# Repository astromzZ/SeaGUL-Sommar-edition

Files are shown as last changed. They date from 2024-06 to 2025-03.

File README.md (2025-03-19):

# Seagul - Chalmers undervattensglidare
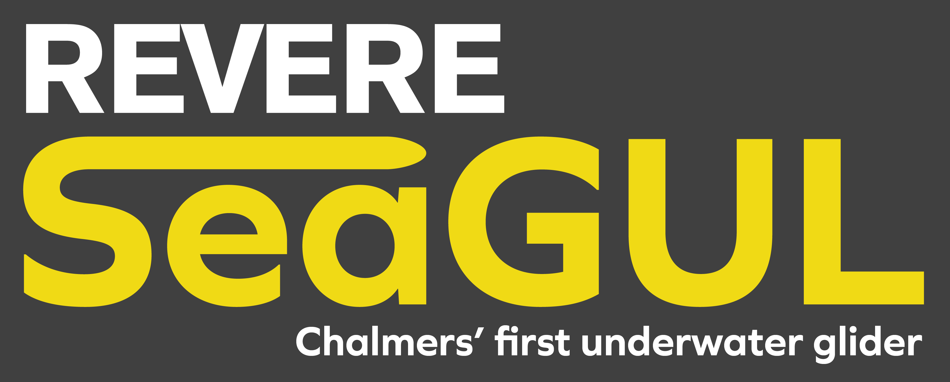
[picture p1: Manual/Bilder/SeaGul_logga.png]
Logga


This repository is for Chalmers underwater glider SEAgul. Here you will find code, instructions and construction files for the glider.

Before handling the glider, make sure to read thorugh the manual. 

The most recent CAD files can be found [here](https://drive.google.com/drive/folders/1H2lXxEGizccBVgk5y8HHm3Ga0hIDHSA2?usp=drive_link).

Contact information:

Oskar Andersson - Oskar.simon.andersson@gmail.com (Programming, CAD)

Peo Gradin - peo.gradin@live.se (Electronics, Programming)

Joel Janson - joeljanson19@gmail.com (Hardware)

Cevin Åström - cevinastrom87@gmail.com (Programming)

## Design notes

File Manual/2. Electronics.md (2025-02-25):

# Electronics

## Overview

he electronic system is divided into three custom-designed circuit boards, as well as several sensors and devices connected to them. The circuit boards are categorized as the "Control PCB," "Power PCB," and "Dropweight PCB." The Control PCB houses the microcontroller, SD card writer, stepper motor drivers, Solid State Relays (SSR) for the pump module, and a series of connectors for connecting the various system components. The Power PCB contains the DC-DC converters and outputs 24V, 3.3V, and 12V voltages. It also includes a voltage divider for measuring battery voltage. The Dropweight PCB technically didn’t need to be a separate circuit board, but it was created to simplify the development of the circuit boards and expedite the completion of the other boards without a finalized dropweight circuit design. The Dropweight PCB controls the electro-permanent magnet through either a signal or a voltage drop in the 3.3V line. The different PCBs and their functionality will be described below. The electronics designs have all been developed using Autodesk Fusion, and the files can be found in the *Electronic files* folder, possibly containing minor changes from the versions that were ordered and implemented in the glider.

## Control PCB

In this section, the control PCB will be presented and explained, hopefully to necessary extent for future improvements and user purposes. Below is an image of the control PCB taken from Autodesk Fusion.

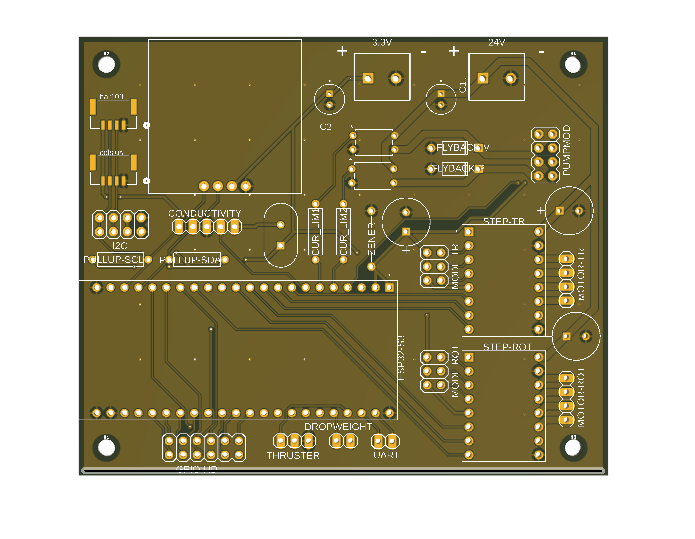
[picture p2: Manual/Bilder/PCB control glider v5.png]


And the schematic design, also from fusion, below.

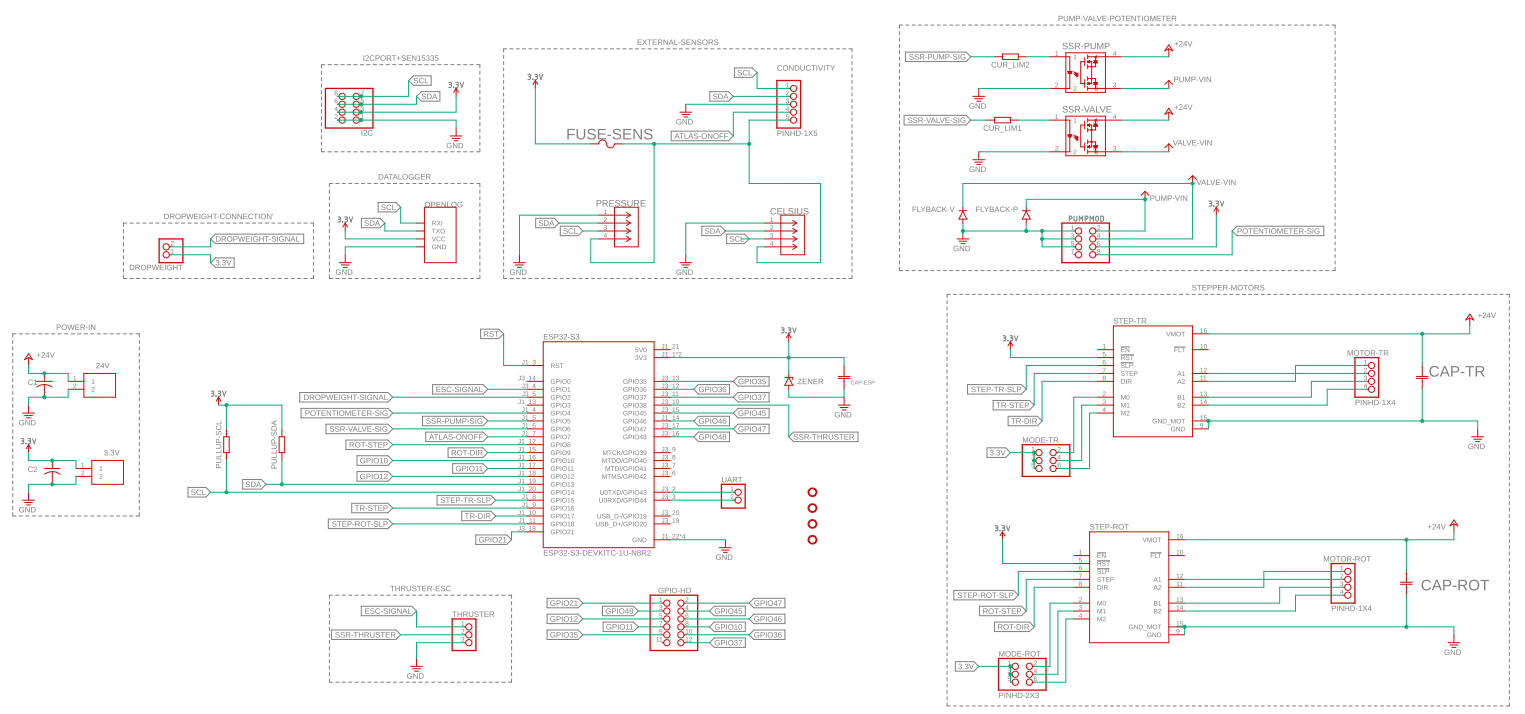
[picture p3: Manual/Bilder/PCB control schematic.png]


Finally we have an image of the control PCB mounted in the electronics bay with all the cable connections, taken shortly after the first water test at Voice of The Ocean (VOTO) with the new system. The USB cable is connected to the ESP32, but otherwise this setup is the same as when the glider is up and running.

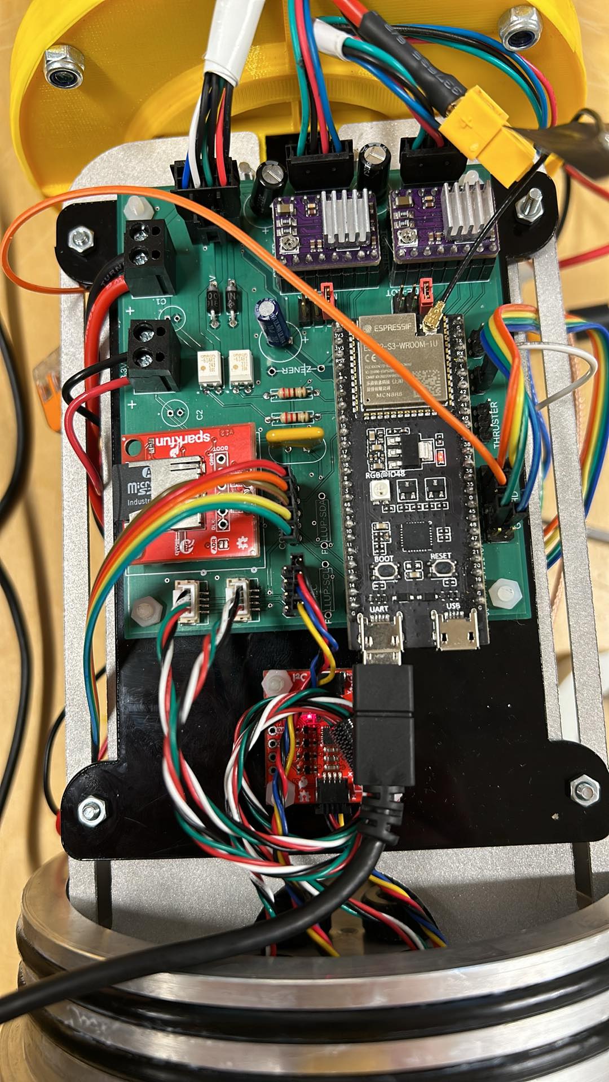
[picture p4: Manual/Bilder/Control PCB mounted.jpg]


### Microcontroller

The control PCB houses an ESP32-S3-DevkitC-N8R8, placed in pin header receptables for easy replacement, that functions as the brain of the system. In addition to communicating with all of the sensors and controlling motors, pump and so on, it also communicates with the Atlas Global Tracker (AGT) module. The AGT handles GPS and satellite communication for the glider, and communicates with the ESP via a Serial (UART) connection. The pinout on the ESP can be seen in the figure below.

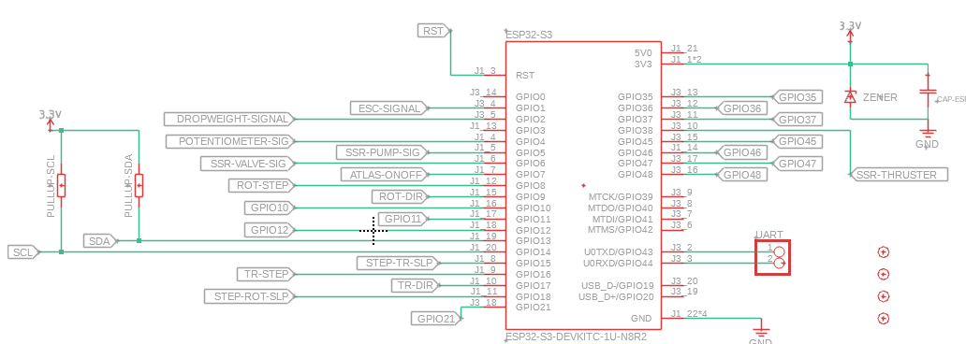
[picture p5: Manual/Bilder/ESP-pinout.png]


Some pins have specific names, and names for their headers, but many of them can be modified to be used for different functions. For example, the UART port can be configured and used as GPIO pins instead. Some other pins are directly traced to PCB mounted components, and not to pin headers, and thus their use can not be modified. An example of this would be the pins used for controlling the SSRs to the pump module. If any modification is to be done, it is advicable to follow the traces on the board in an EDA software, or in the images of this github manual, and make sure that it works as intended.

### GPIO header and other designated pin headers

There are som pins simply drawn out to pin headers on the circuit board, some which are designated for certain purposes and some unused. The GPIO header pinout can be seen in the image below

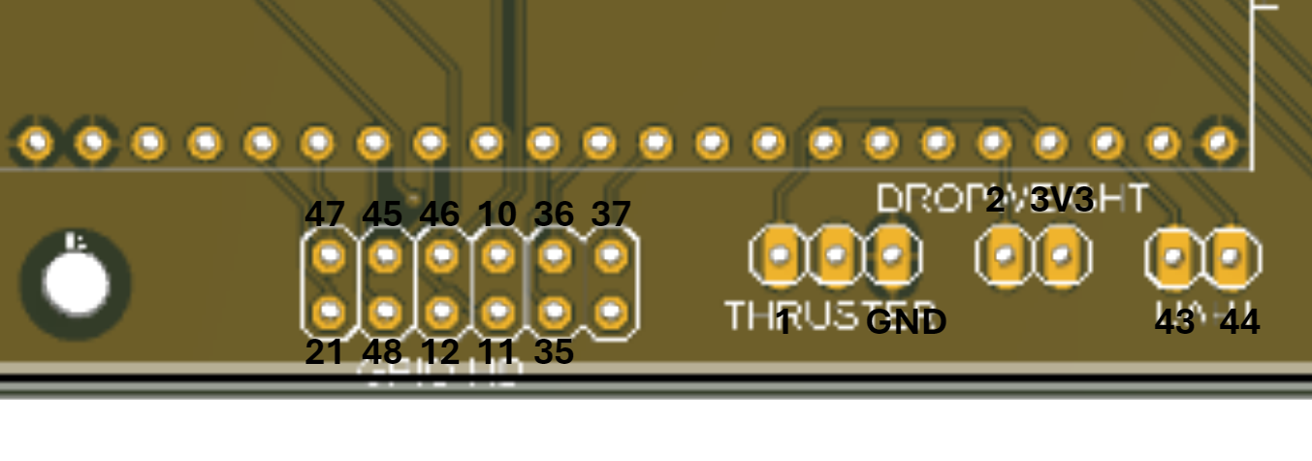
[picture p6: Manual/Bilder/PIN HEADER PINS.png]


where the connections for the thruster, dropweight and UART are also found. The numbers refer to the specific GPIO pin number from the ESP32. Unnamed pins in the image are simply not routed and can be ignored. The UART pins are unused as of now, but could connect to a UART device or be used as GPIO pins. The dropweight header has a signal pin, GPIO2, for the ESP32 to trigger the dropweight system, and also a 3V3 pin which can be used if the dropweight circuit is configured to be able to release the weight in the event of power failure. More on that in the description of the dropweight circuit.

Out of the general GPIO pin header, some are used for specific purposes listed below:

- **GPIO10** is used to read battery voltage, and this needs to be done from an ADC capable pin (preferrably ADC1 since ADC2 can be limited)

- **GPIO11** is sintended to be used to enable the voltage divider for reading VBAT, but is not implemented right now as one of the tranistors used in that circuitry did not work with 3.3V (Explained more in the *power PCB* section) and thus it is unused currently

- **GPIO12** is intended to be used for the SOS leak sensor, but not currently tested and implemented.

- **GPIO35 & 36** are used as Serial (UART) pins in communication between the ESP32 and the Atlas Global Tracker. 35 (TX) is connected to SCK on the AGT, and 36 (RX) is connected to CIPO on the AGT. Note that RX on one device goes to TX on the other device.

- **GPIO45** is connected to the AGT AD35 pin and is used to "poke" the AGT, in order to wake it up and establish communication between the microcontrollers

- **GPIO48** is connected to the AGT D4 pin and is used to recieve a "poke" from the AGT, in the same purpose as for GPIO45.

### Stepper motor drivers

In order to drive the two stepper motors that are used in the maneuvering module to move the center of gravity of the glider, there are two DRV8825s mounted to sockets on the circuit board. Sockets are used for simple replacement. These have an adjustable onboard current limit which is set to the limit of approximately 1.2A, as to not overpower the stepper motors. See https://www.pololu.com/product/2133 for more info.

These stepper motor drivers use three pins each from the ESP32; STEP, DIR and SLEEP. Sleep mode is used when the motors are not running in order to minimize energy use.

Furthermore, there are 3x2 pin headers connected to the DRV8825's MODE pins in order to control the microstepping mode. For info on how the microstepping is set, see https://www.pololu.com/product/2133. Simply place pin header jumpers over the pins in order to bridge the 3.3V line to the desired MODE pins on the driver. This can be seen in the image below, where the red jumpers are placed such that both stepper motors are in the 1/16 microstepping mode.

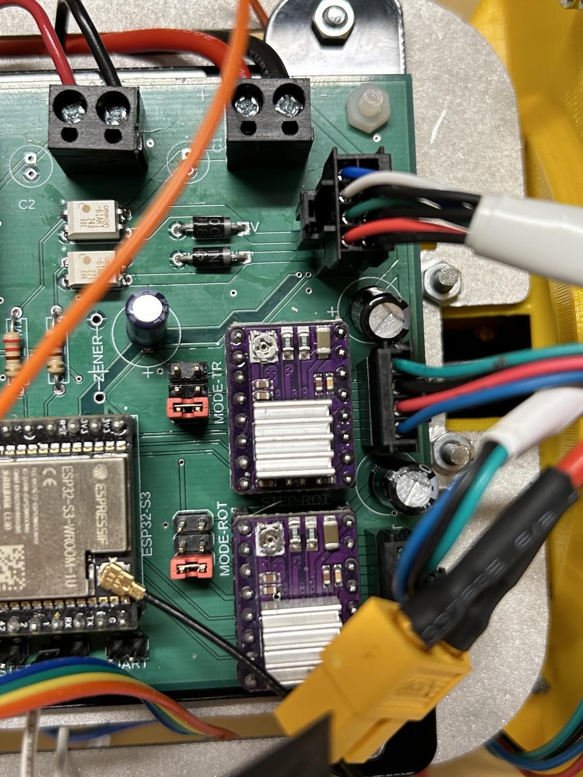
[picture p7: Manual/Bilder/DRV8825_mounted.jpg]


From the view of the picture above, the left columns of the pin headers are connected to the 3.3V line, and the right side columns are connected to the MODE1, MODE2 and MODE3 pins respectively.

Near the input VMOT, which is 24V, to the DRV8825's are 47 $\mu F$ electrolytic capacitor to help reduce voltage spikes and noice, to protect components. And the stepper motors are connected with Molex NANOFIT 1x4 connectors mounted to the circuit board.

### Variable bouyancy engine

The variable bouyancy engine consists of an internal reservoir and an external bladder, between which hydraulic oil flows in order to control the gliders bouyancy to make it dive or float. To move the hydraulic oil to the external bladder, there is a geared micropump from TCS (https://micropumps.co.uk/product/mgd1000p-pk-v/) with it's own control board (EQI-UART), used in a configuration where the pump runs at constant speed set by an on board potentiometer on the pump driver. When the oil is moved to the reservoir instead, there is a solenoid valve (Burkert Solenoid Valve 134084) that combined with the internal vacuum of approximately -0.3 bar can transport the oil in from the bladder. In order to check the amount of oil in the reservoir, there is a SoftPot potentiometer mounted to the module as seen in the image of the whole VBS below.

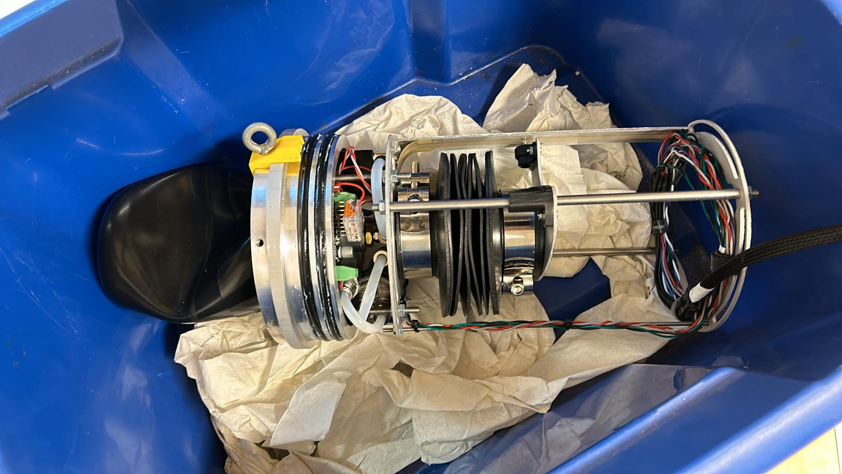
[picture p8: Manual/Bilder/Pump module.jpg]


Both the pump and the solenoid valve are controlled from the microcontroller via Omron G3VM 61AR1 solid state relays, with ~180 $\Omega$ current limiting resistors connecting the controlling pins to the SSRs. This mode of controlling pump and valve allows for easy implementation with control only by writing one pin high or low respectively, and builds on earlier work. The EQI UART control board for the pump can be configured for more advanced usage, but for simplicity the system has been kept in the "one speed" configuration.

The connection to the VBS is made through a Molex NANOFIT 2x4 connector mounted to the board, with the physical layout and pins shown below. Note that there is also flyback diodes in place near the pump and valve connections, in order to handle the back-EMF that can occur in inductive loads such as these. They can be of importance to protect the SSRs from sudden voltage spikes from afforementioned back-EMF, especially when switching the pump or valve on and off.

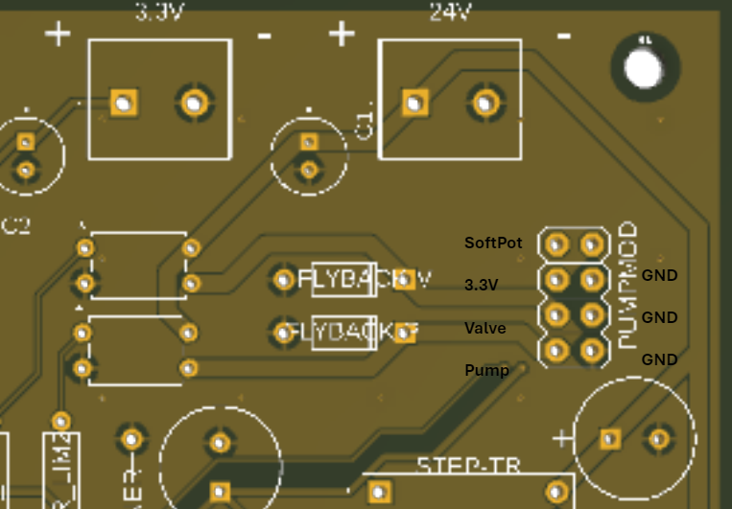
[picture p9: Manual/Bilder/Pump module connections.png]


The cable is drawn all the way through the glider from the electronics bay to the pump module, which should be connected before mounted. The cable could be modified if one for some reason wants the pump module to be mounted in the hull before the back aluminium lid containing the electronics bay, but we've found this to be the easier way.

### Power lines on the control PCB

There is not much to be said about the power lines on the control PCB, since it is fairly simple in design. One thing to note is that there is, currently unpopulated, slots for placing additional decoupling capacitors on both the 3.3V line and the 24V line. These leave room for mounting capacitors in case there is unwanted noise, but as of now it has not been found necessary.

Furthermore there is a 10 $\mu F$ electrolytic capacitor mounted closely to the ESP32 to protect it from voltage spikes, and there is also a slot for mounting a zener diode right next to it, which has not been done yet. If a zener is mounted, a 3.5V zener would probably be the best. The value should be below 3.6V since the microcontroller can't take a higher voltage, and it should be above 3.3V in order to not waste energy continuously during operation. This protection is needed since there is no internal voltage regulation on the ESP32 when it is powered via the 3.3V pins as it is now.

 The connections for the power lines can be seen in the image showing the pump connectors in the previous subsection. The power is connected via cables that are mounted in screw terminal blocks on the circuit board, connecting to the power PCB.

 ### Sensors and SD card module

The glider uses a temperature sensor, pressure sensor, electrical conductivity sensor, an SD card module and an IMU to both control the system and save gathered data. Currently they are all connected to the ESP32 via the I2C protocol.

The temperature sensor is a Blue Robotics Celsius-Fast-Response, and the pressure sensor is a Bar100 also from Blue Robotics. Both of these are connected directly to the board via JST GH 1x4 connectors in order to be compatible with the original cables for the sensors. This makes for easy integration without modifying cables, and also makes it simple to switch out sensors or use the glider's sensors for other projects if needed.

The SD card module is a SparkFun Qwiic OpenLog, that is mounted on to the board in a socket header, via its soldered-on pins. The sockets once again makes it easier to switch out a faulty model.

The conductivity sensor is an Atlas Scientific Mini Conductivity K1.0 that can read the electrical conductivity, salinity and total dissolved solids (which all are linearly dependent, so it's really just the electrical conductivity that is physically measured and then scaled with proportionality constants). This sensor has it's own controller board, that is mounted in between the two aluminium plates of the electronics bay, and is connected through a pin header.

In the below image we can see the part of the circuit board which houses the OpenLog and the sensor connectors. Note that there is a slot to the right of the conductivity pin header which houses a 0.33A resettable fuse that protects the conductivity sensor as well as the Blue Robotics sensors. The fuse does NOT protect any of the other sensors, or 3.3V circuitry in general.

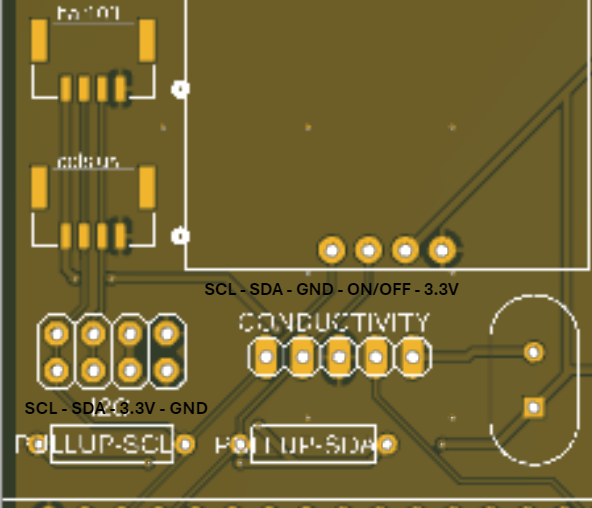
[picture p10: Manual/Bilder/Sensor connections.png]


There are also slots in place for pullup resistors on the I2C clock and data lines (SDA, SCL) but these are currently unpopulated. Typical values of pullup resistors seem to be around 1 - 10 $k \Omega$ but we have not identified a particular need for this. The option remains to solder on resistors here if it would be deemed necessary in the future.

The IMU that is used for the glider is a SEN-15335 from SparkFun, that is connected to one of the two rows of the I2C header that can also be seen in the image above.

It is worth to note that the conductivity sensor also has an option for ON/OFF, in other words a SLEEP mode with lower current draw. However this is not implemented currently, since the sensor is measuring continuously during the gliders operation. If needed, this could simply be connected along with the other connecting jumper cables and in software in order to save energy, as this sensor is probably the one with highest current consumption.

## Power PCB

In this section the power PCB will be explained. This circuit board connects to the battery and via DC-DC converters outputs 24V, 3.3V and 12V. Below you will see the schematic and images of the PCB design, and in the coming subsections the design will be explained in further detail.

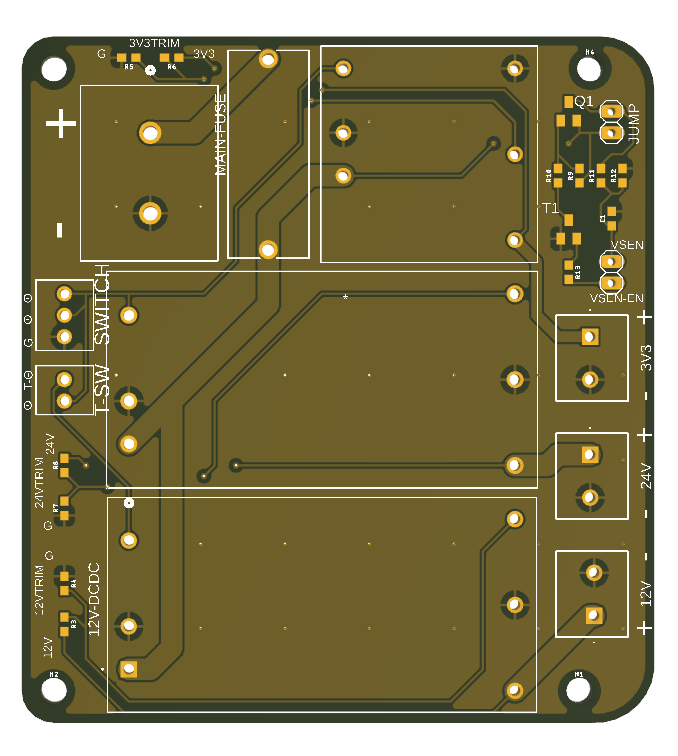
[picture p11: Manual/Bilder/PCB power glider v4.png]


The image above shows a 3D rendering snapshot of the full power PCB. Note that by mistake, the mounting holes are not positioned correctly in a square pattern. This should be corrected if any new revisions of the circuit board is developed.

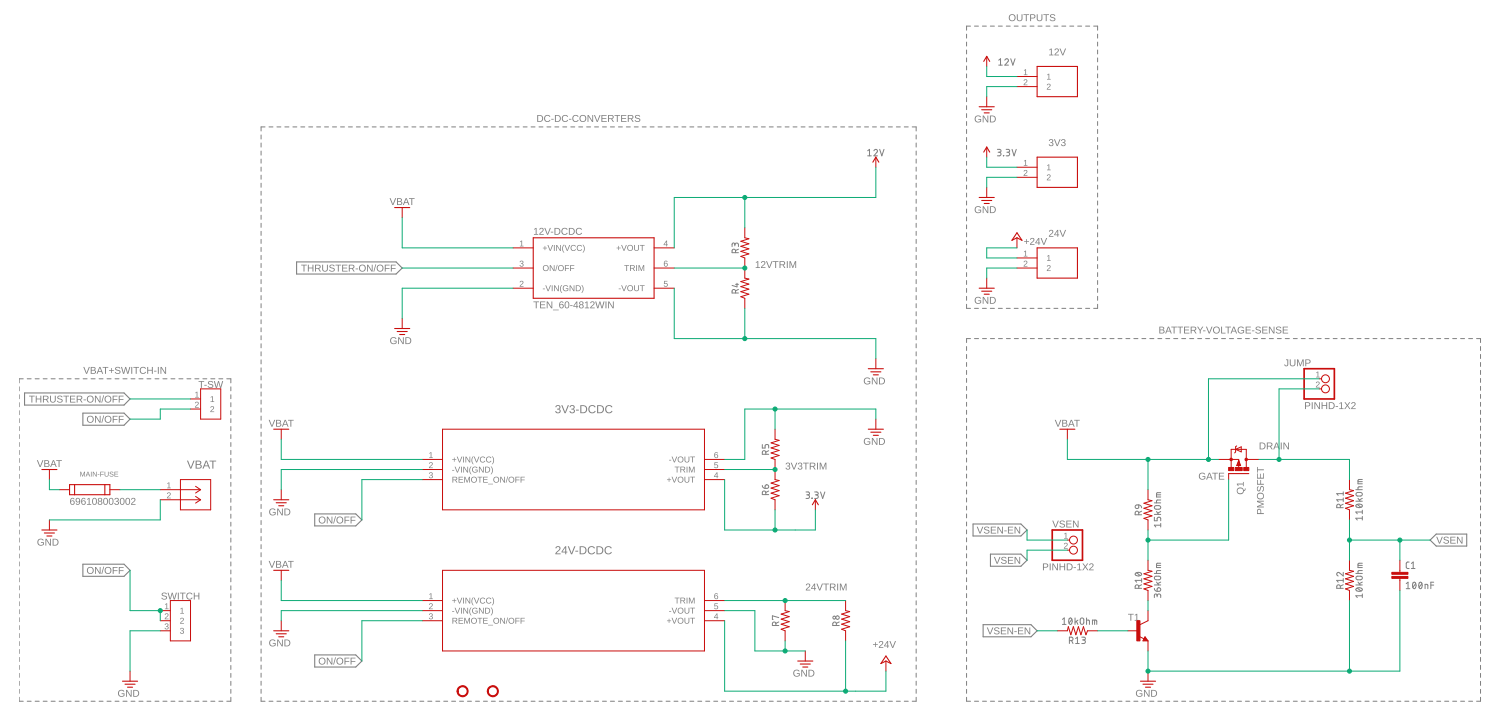
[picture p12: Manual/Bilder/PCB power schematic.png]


The image above shows the full schematic design of the circuitry, and finally the image below shows the PCB mounted in the glider

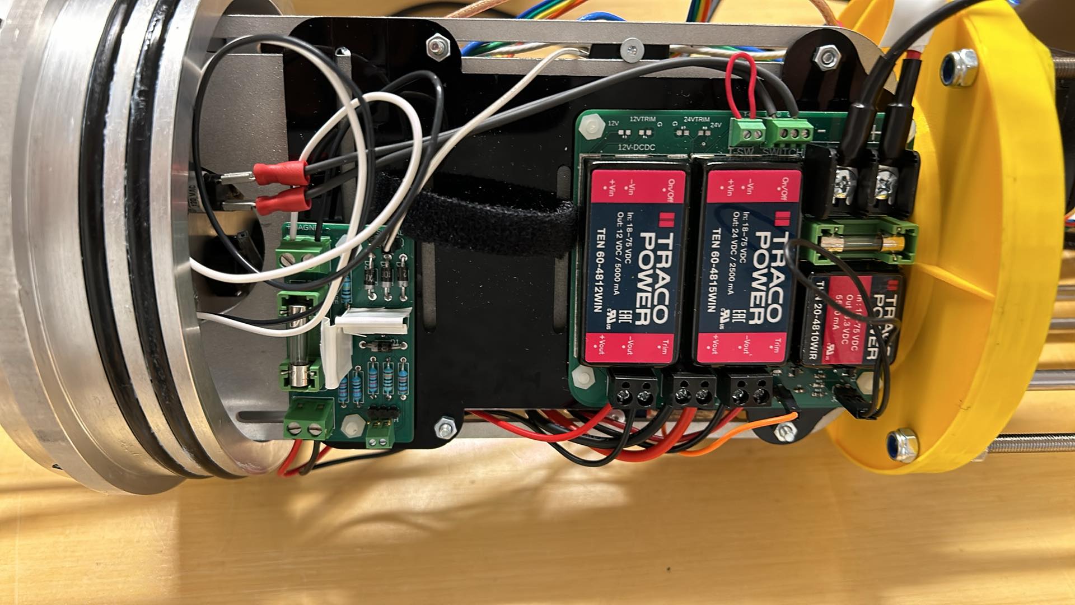
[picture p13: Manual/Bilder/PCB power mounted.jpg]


### Power input and DC/DC converters

The power from the battery, or other power source, is connected to the board via a board mounted screw terminal barrier block (10mm pitch). The connected power source needs to provide 18V-72V for the DC/DC converters to work correctly, otherwise you might not get any output voltages at all. The power input then goes directly to the 5x20 cartridge fuse holder. The cartridge fuse that has been used is a 3.15A fuse, but it can be easily removed and replaced. This is the only fuse apart from the resettable PTC fuse for the sensors, since fuses take up a lot of space and also dissipate power. 

After the fuse, the power goes through the DC/DC converter whose output goes their respective to 5mm pitch screw terminal blocks to be connected to the other circuit boards.

All of the DC/DC converters are from TRACO and are of high quality. They are isolated converters, but in this implementation the ground has been chosen to be the same for all circuitry. This is because separated grounds can cause issues if a device uses both 24V and 3.3V for example, as is the case with the stepper motor drivers. The 24V converter is a TRACO TEN 60-4815WIN, the 12V converter is a TRACO TEN 60-4812WIN (https://www.tracopower.com/int/series/ten-60win) and the 3.3V converter is a TRACO THN 20-4810WIR (https://www.tracopower.com/int/model/thn-20-4810wir).

### Switch

Since the DC/DC converters have their own on/off switches (remote ON/OFF pins), this has been used in order to switch the power on and off. This might not be the most power efficient method, but it keeps the number of components down and doesn't take up any further space on the board, which a separate load switch with for example power MOSFET's would do. It can be noted that when powered via a DC lab power source, the leakage current has been below 1 mA when switched off, and the power dissipation would only be noticable if the battery was connected with the glider switched off for long periods of time, which should not be an issue in any case.

The on/off input for the converters are voltage controlled, and typically 0-1.2V or a short circuit to ground powers them down, and 3-12V (3-15V on the 3.3V converter) or an open circuit powers them up. In this circuit board, they are powered down by connecting the on/off pins to ground, and depending on the configuration they are powered up either by a voltage or switching to an open circuit (such that the on/off pins are not connected to anything).

The switched used right now is mounted in a blue robotics switch module (https://bluerobotics.com/store/comm-control-power/switch/switch-10-5a-r1/) which off the shelf comes with a Grayhill 30-3UL switch that can handle 26V and 5A. However the 30-3UL and similar switches have sensitive connection spokes, and one of them broke. Therefore it was replaced with a Grayhill 30-6UL switch. The difference between these two are that the 30-3UL is normally open (NO) and the 30-6UL is normally closed. Basically their function is completely opposite of each other, which means they can't be used and connected in the glider in the same way.

As mentioned, right now the 30-6UL switch is used, and this is connected to a terminal on the PCB with one side connected to ground, and one side to the on/off pins. When the switch is on, it disconnects the on/off pins from ground, and when the switch is off it reconnects the on/off pins to the ground. Furthermore, for the 12V converter there is an option of either connecting it to the 3.3V and 24V converters on/off pins and have them all switch on and off simultaneously, or controlling it directly from the microcontroller. The design purpose of these two options is that if the 12V circuit powers only the thruster, it can be turned on and off via the microcontroller based on when the thruster is used. Otherwise, if the backup battery is not used the 12V converter can be used to power the dropweight circuit, in which case one would want the converter to be operating at all times. This is the option that has mainly been used during the gliders testing at the time of writing. It is however worth to note that the DC/DC converters consume around 6 mA in order to operate, and thus using the backup battery for powering the dropweight circuit is more energy efficient.

With the 30-3UL, the switch would have to be connected in a way that when switched on, it gives a voltage between 3V and 12V and when switched off it gives 0V. This can be done when a backup battery is used to power the dropweight circuitry and the switch is connected directly to the dropweight PCB, and further routed to the on/off pins of the DC/DC converters. This will be further explained in the dropweight PCB section.

In the image below, the switch connections on the PCB are shown. The inputs with the "on/off signs" go to the 3.3V and 24V on/off pins directly, and the "G" sign denotes a ground connections. The T-on/off sign is for the input of the on/off pin of the 12V converter, which when connected to the on/off sign right next to it becomes connected to the 3.3V and 24V switch pins, making all the converters switch simultaneously.

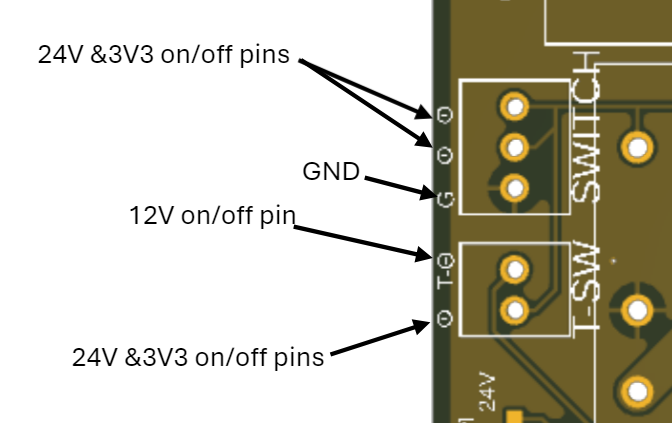
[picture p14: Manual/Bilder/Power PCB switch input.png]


### Voltage adjustments

The high quality TRACO DC/DC converters all have the option of adjusting the output voltages by some margins. For more info on the exact adjustments that can be made, see their respective application notes and/or datasheets. In simple terms, to adjust the voltage upwards you connect the TRIM pin to the positive output VOUT+ (24V, 3.3V or 12V respectively) via a resistor of some value, and to adjust it downwards you connect the negative output VOUT-, which in all these cases are simply GND, to the TRIM pin via a resistor. Since this has not been needed so far, none of the outputs have been adjusted, but there are slots available to simply solder on surface mount 0603 resistors if needed in the future.

For reference the image below shows the slots for resistor where the 12V and 24V converters outputs can be adjusted by soldering on resistors. If this is to be done, make sure to get the correct resistor values from the application notes of the converter, and solder it either to the positive output slot or the ground connected slot, never to both.

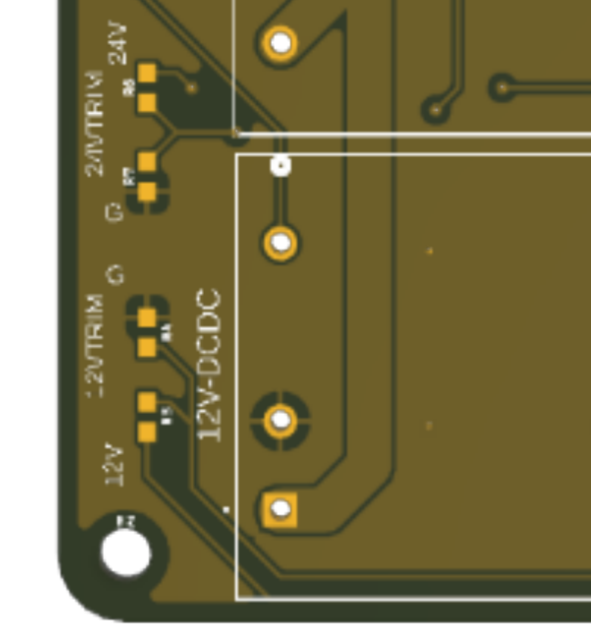
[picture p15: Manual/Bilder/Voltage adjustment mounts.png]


### Voltage divider for measuring battery life

The method of measuring battery life in order to not run out of battery during the gliders operation is based on simply measuring the voltage of the battery. This method is based on the fact that lithium ion  batteries have a discharge curve where the voltage is decreased as the remaining capacity of the battery decreases. By having a minimum allowed voltage before the glider resurfaces and signal to land that it needs to be picked up, one can ensure that it doesn't completely discharge the batteries and is lost due to a power loss. This function is not completed and tested in the software just yet, but the needed hardware in order to measure the battery voltage is there, and that is what will be described here.

The voltage sensing circuit measures to voltage after the main fuse, going towards a configuration of transistors meant to be able to switch the battery sensing circuit on and off based on a 3.3V signal VSEN-EN from the microcontroller. However, in this case the transistors mounted did not work as expected and would have to be switched out for this function to work. There is a workaround, by setting a jumper cable over the 2-pin header that bypasses the PMOSFET labeled Q1, the current is closed and VSEN can be used to measure voltage. In this configuration, the circuit will always be drawing a small amount of energy, so one should disconnect the jumper cable bypassing the Q1 PMOSFET whenever the glider is not active. The schematic of the circuit can be seen below

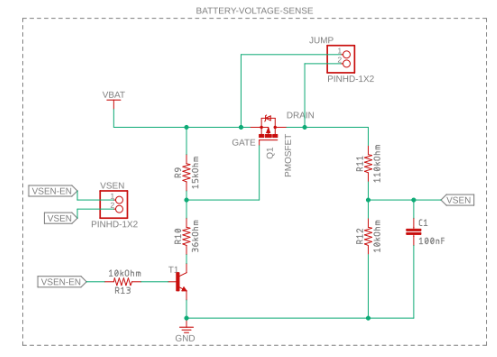
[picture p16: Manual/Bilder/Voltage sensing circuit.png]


The error with the circuit in regards to the transistors, is probably that the BJT transistor labeled T1 demands a higher voltage than 3.3V in order to switch on, and it would have to be switched out for proper function.

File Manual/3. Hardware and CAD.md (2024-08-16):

# Hardware

In 2024, a large part of the mechanical construction and hardware was carried out in collaboration with Pelle Evensen and Henrik Hörlin at FUSE, Chalmers. 

## Rear lid

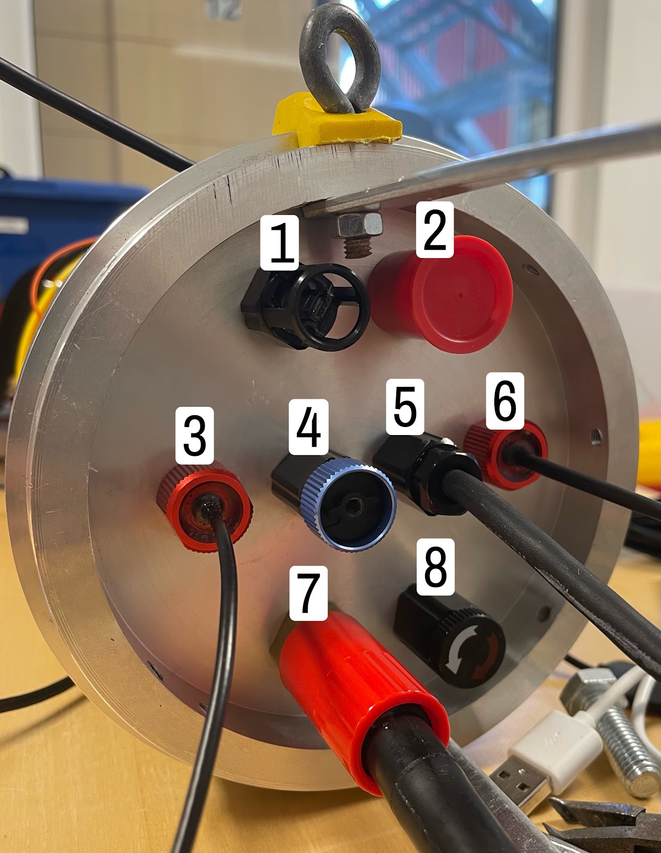
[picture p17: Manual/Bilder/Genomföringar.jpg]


A cylinder in aluminum with 150 mm diameter was turned to desired design.
Eight different penetrations were made in the rear lid by first drilling with a 9,8 mm drill. Next, one of the holes was threaded to 7/16 inch to fit a SubConn bulkhead of the same dimensions while the remaining penetrations were reamed up to 10 mm to fit M10 screws.
The penetrations in the rear lid are used for the following purposes:

1. Temperature sensor (M10)
2. Pressure sensor (M10)
3. Salinity sensor (M10)
4. Vacuum valve (M10)
5. Thruster (M10)
6. Antenna (M10)
7. Dropweight (7/16” 20 UNF)
8. On/Off switch (M10)

<br clear="right"/>

In addition, radial holes were drilled in the lid. With 45 degrees of separation, seven M5 holes and one M6 hole were drilled and threaded. A ninth radial hole was also drilled and threaded into M6, to mount the sacrificial anode. The radial holes were distributed using a dividing head at Microfabriken.

## Pump module

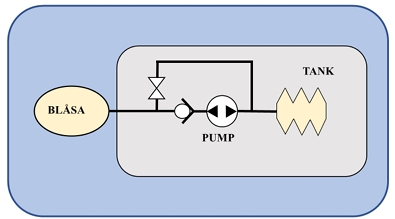
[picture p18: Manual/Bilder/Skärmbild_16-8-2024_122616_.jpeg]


The pump module consists of an internal bellow and an external bladder. To change the gliders effective volume, hydraulic oil is being transferred between these two bladders. A pump is used to fill the external bladder through a one-way-valve. The negative pressure in the glider is used in order order for the oil to return to the internal bellow. This is allowed by opening a magnetic valve. A potentiometer is used to monitor the bellows' oil level.

The mechanical construction of the pump module was conducted by the bachelor thesis in 2023. 

The original hydraulic oil used in the pump system had ISO viscosity grade 116 cSt ([rs-online/hydraulic-fluid-116](https://se.rs-online.com/web/p/hydraulic-fluid/2044572?gb=s)). The magnetic valve is only rated for viscosity ≤ 20 cSt so this oil was actually way too thick for the system. Currently the oil being used has ISO viscosity grade 15 cSt which runs much better ([mekster/mpm-hydraulic-oil-15](https://www.mekster.se/mpm-15-hvi-15-842747.html#918=115189)).

<br clear="right"/>

## Aluminum rack
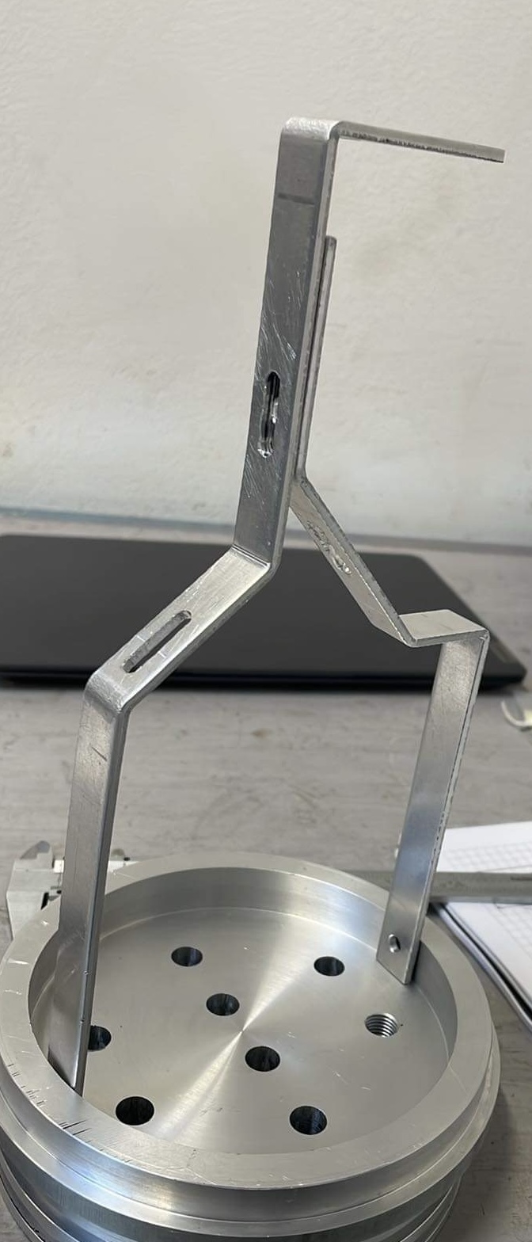
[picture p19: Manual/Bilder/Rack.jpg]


Mounted on the rear lid is an aluminum rack that holds the antenna, the thruster and the magnet for the dropweight. The rack is made by cutting out 3 mm thick aluminum sheet to 15 mm wide strips and then bending to the desired shape. The holes in the rack are drilled to fit M5 screws.
<br clear="right"/>

## Electronic mounting plates

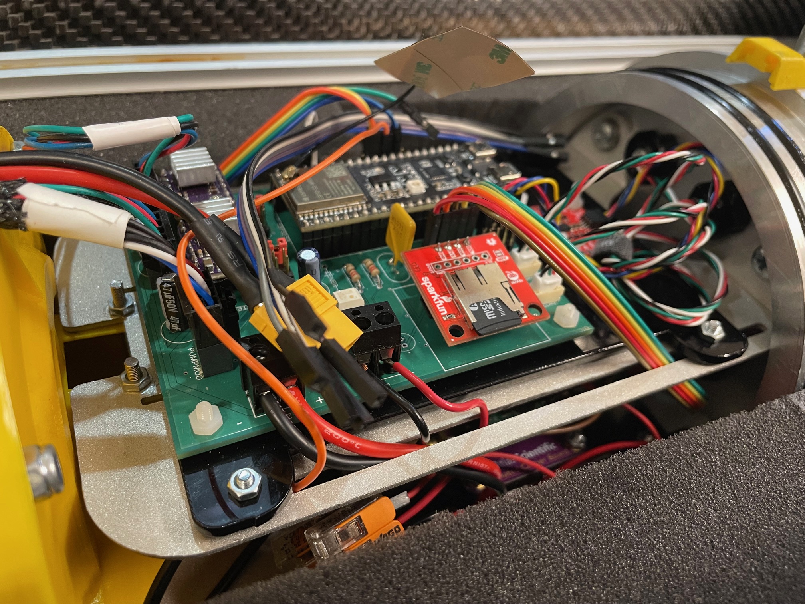
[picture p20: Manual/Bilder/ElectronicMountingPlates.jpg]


To mount electronics inside the glider, mounting plates were created in 2 mm thick aluminum sheet. They were cut out with a water jet at FUSE and then sandblasted to achieve a nice surface. Finally a sheet metal bending machine was used to bend the mounting plates.

The PCBs are not directly mounted on the aluminum plates but are instead placed on black acrylic mounting plates. These have been cut out with a laser at CASE.
<br clear="right"/>

## Maneuvering module

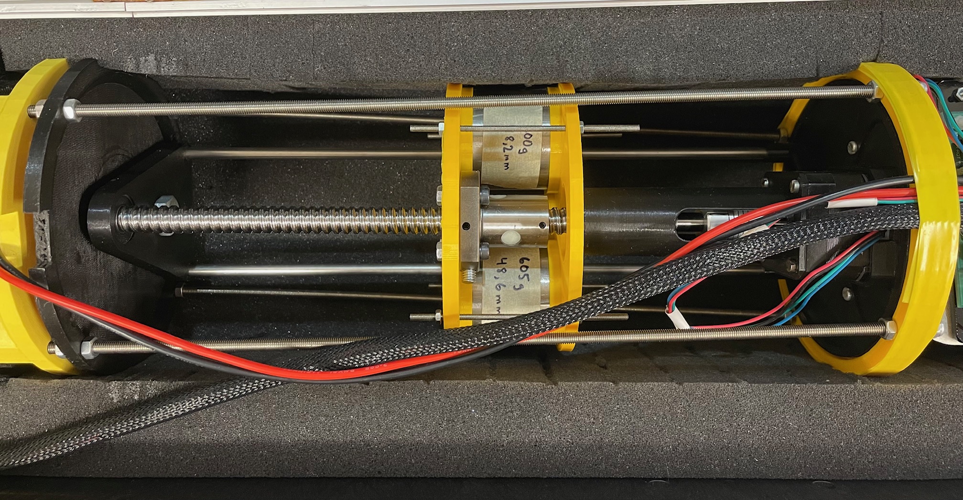
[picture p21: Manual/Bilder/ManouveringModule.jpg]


The maneuvering module enables the movement of internal weights in the glider. The weight package consists of three steel cylinders weighing about 600 g each. A ball screw driven by a stepper motor can move the weight in translational direction while another stepper motor can rotate the weight package.
<br clear="right"/>

## Battery module

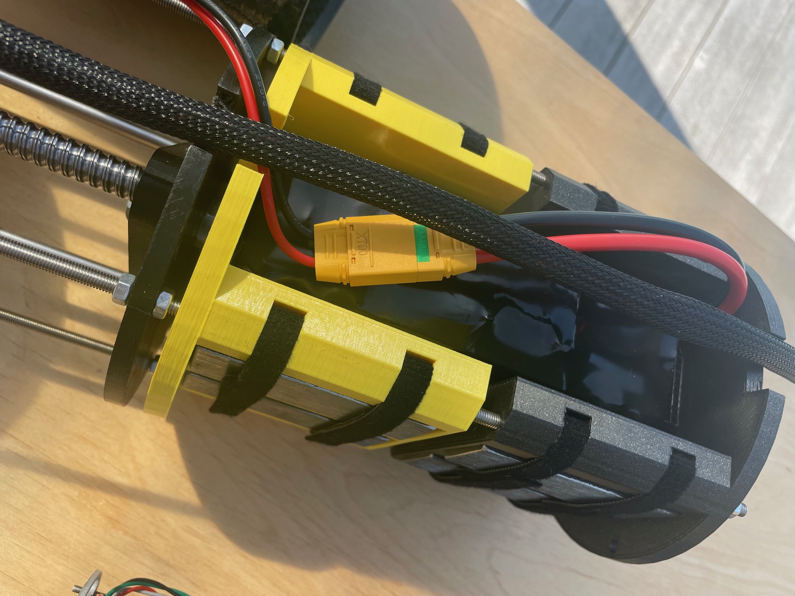
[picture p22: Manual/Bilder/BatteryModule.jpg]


The battery module was designed to accommodate space for one battery as well as space for ballast. On the sides, 12 steel rectangular blocks can be clamped, each weighing about 300 g. Furthermore, there are two steel plates with dimensions of 170x60x3 mm, weighing about 235 g each, which can be placed under the battery for additional ballast. 
<br clear="right"/>

## Antenna
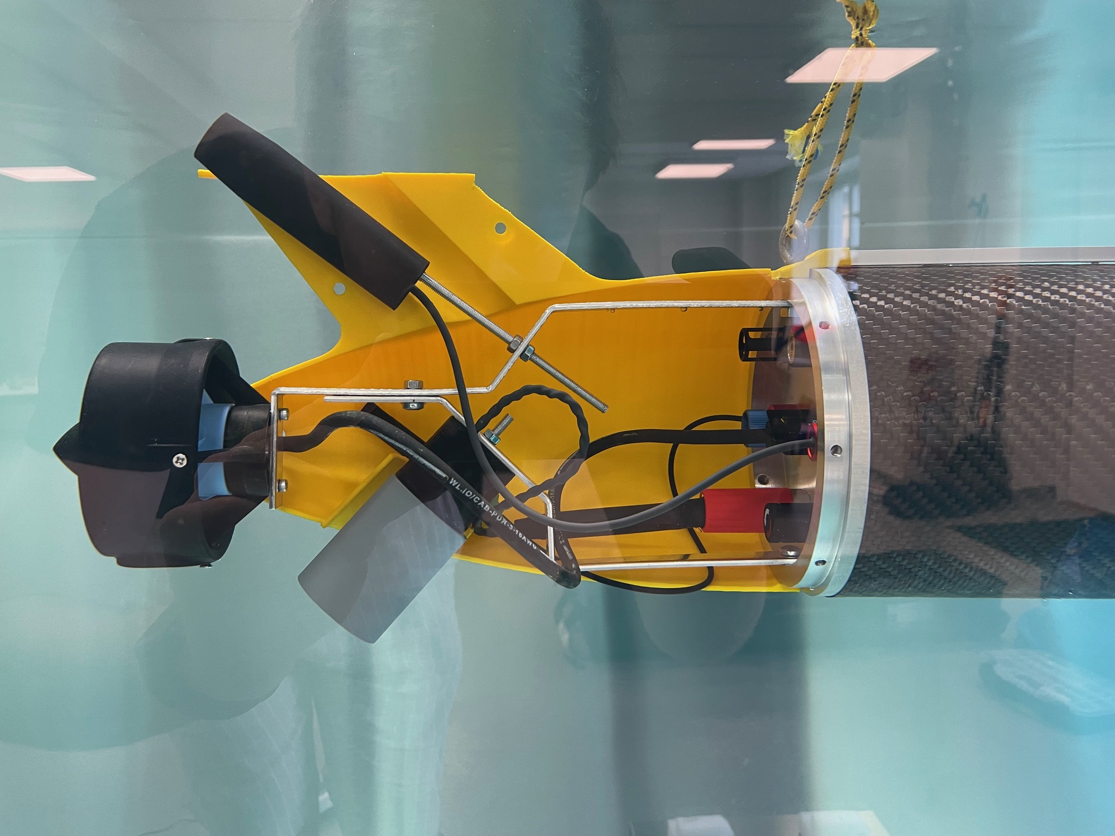
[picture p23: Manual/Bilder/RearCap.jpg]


The antenna has combined purpose in that it provides communication via both GPS and Iridium. The antenna was placed in a molding socket together with a threaded aluminium bar and then molded together using epoxy. This ensures that the antenna is waterproof and that it can easily be mounted to the aluminium rack. In order to have a waterproof penetration for the cable through the rear lid, epoxy was once again used to make a potted penetrator.

## Dropweight

The dropweight system consists of an electropermanent magnet that holds a cylindrical weight. To waterproof the electrical contacts between SubConn and the magnet, heat shrink tubing was first used around the wires. Next, a molding socket was used to mold the cable to the SubConn connector with epoxy. 

The SubConn cconnector was ordered from MacArtney. Emil Andersson ([ean@macartney.com](ean@macartney.com)) at MacArtney is a good contact person when it comes to underwater applications which can be relevant for the glider.

The magnet was also molded in epoxy to be waterproof. On the magnetic surface, a very thin layer of epoxy was used to try to obtain as much magnetic strength as possible. The magnet was later spray-painted black and lacquered for both aesthetic reasons and to have a slightly more durable surface. 

The actual dropweights are steel cylinders with 50 mm diameter. To prevent corrosion, the weights were treated with zinc spray, which acts as a sacrificial anode. Note that not all dropweights have been treated since the zinc spray ran out. In the future it might be preferable to electrogalvanize the dropweights instead for improved durability.
<br clear="right"/>

# CAD

CAD-files can be found under [README.md](/README.md)

3D-printing have mostly been performed at CASE but also to some extent at 3D-labbet in the physics building and at Revere. Every part has so far been printed in PLA but it is strongly recommended to print a new front cap, end cap, wings and holder for the wings in PETG. PLA will deteriorate in saltwater whereas PETG will hold up much better over long periods of time.

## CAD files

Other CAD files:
Manual/Electronic files/Dropweight PCB/dropweight_test v15.f3z
Manual/Electronic files/Power PCB/PCB power glider v29.f3z

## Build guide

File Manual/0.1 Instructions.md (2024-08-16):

# Instructions
The following page contains instructions which are neccesary for development and use of the glider.
# Programming
## Intro

The code for the glider has been developed with the Arduino programming language through the arduino extension in VScode. The programming encompasses both code for the main micro controller (ESP32-S3) and the Artemis Global Tracker, which together makes the glider function.

Some useful links for programming:
- [Sparkfuns repository for the ATG](https://github.com/sparkfun/SparkFun_Artemis_Global_Tracker), it contains alot of useful examples.

## Programming setup

### Software
For the programming to work for the glider, a few steps are needed. First off you need to be able to have easy access to the github repository, the most simple way to do this is to download the Github Desktop app and follow online instructions to copy the repository toyour computer. From there you can pull changes others have made and push your own contributions. Secondly you will need a code interface, for this you should use VScode. From github desktop you will be able to link your VScode to sync your changes. 

### VScode
Your VScode will need some work before functioning properly.

1. In the extensions manager, download the Arduino extension.

2. Follow [online instruction](https://dev.to/gamegods3/how-to-install-gcc-in-windows-10-the-easier-way-422j) to download the g++/gcc compiler. 

3. Open one of the larger files eg. *glider_monterat_test3*. All of the **#includes** will be marked red, this is due to missing libraries. Click *ctrl-shift-p* and find the arduino library manager. From there you will be able to start downloading libraries which include the different header files. Some of the libraries can be hard to find, but shouldnt be more than a google search away. These libraries will probalby endup in *C:\Users\<YourUsername>\Documents\Arduino\libraries*

4. Now you will need to download the right board setups. go to ctrl-shift-p and search for **ESP32** and add that. Next do the same for the **SparkFun Apollo3 Boards**. Now you will be able to find the correct boards in the bottom right corner of VS code (**ESP32S3 Dev module** and **RedBoard Artemis ATP**).

### Using the boards
Before uploading code to the microcontrollers you will also need to go though some steps.

#### ESP32S3

1. Plugg in the microcontroller with a micro-usb cable using the 'UART' port. 
2. Change the **COM** port in VScode in the bottom right corner. VScode should only show you one option (eg. **COM4**). 
3. Change the board type to **ESP32S3 Dev Module**.

4. Change the programmer to **Esptool**

5. **Verify** the code in the top right corner. If any issues appear, resolve these (see troubleshooting section furhter down). 

6. If verified correcly hold down the **boot button** on the ESP32 and uppload using the **uppload button** in VScode. When this text appears, **release** the boot button:
> Sketch uses 1037061 bytes (79%) of program storage space. Maximum is 1310720 bytes.
Global variables use 44136 bytes (13%) of dynamic memory, leaving 283544 bytes for local variables. Maximum is 327680 bytes.
>

#### Artemis Global Tracker, AGT

1. Plugg in the microcontroller with a usb-c cable.

2. Change the **COM** port in VScode in the bottom right corner. VScode should only show you one option (eg. **COM4**). 

3. Change the board type to **RedBoard Artemis ATP (SparkFun Apollo3 Boards)**.

4. In the Board Configuration change the Baud Rate to **921600** and make sure the uploader in SparkFun Variable Loader. 

5. Change the programmer to **Ambiq secure bootloader**

6. **Verify** the code in the top right corner. If any issues appear, resolve these (see troubleshooting section). 

6. If verified correcly begin the upload. 

## Trouble shooting
With the setup complete there will still unavoidably be some issues, there are some known issues and some which will be unique to your computer and its setup.

### Known issues
For the ESP32 to work properly it may be neccessary to add **USBCON** and **ARDUINO=10812** to the *c_cpp_properies* file under *defines*, for more context see the code block below.

### Standard trouble shooting
The most common issue is pathing to the libraries in VScode. You may need to include the libraries manually or change the directories yourself. The added libraries can as previously mentioned be found in *C:\Users\<YourUsername>\Documents\Arduino\libraries* and the standard libraries should be found in *C:\Users\<YourUsername>\AppData\Local\Arduino15*. In these directories you should be able to find the header files which are missing and manually add them to the force include. 

### c_cpp_properties.json
This file will be created the first time you compile a sketch adn create an intellisense configuration. It is here you change searched directories and other preferences. Bellow follows a snippet of an example **c_cpp_properies** that has had some troubleshooting steps. Your file shouldn't necesarilly look like this, this is just an example of how it could look after some manipulation:

    {
    "version": 4,
    "configurations": [
        {
            "name": "Win32",
            "compilerPath": "C:/MinGW/bin/gcc.exe",
            "compilerArgs": [],
            "intelliSenseMode": "gcc-x64",
            "includePath": [
                "${workspaceFolder}/**",
                "C:/Users/oskar/AppData/Local/Arduino15/packages/esp32/**",
                "C:/Users/oskar/AppData/Local/Arduino15/packages/arduino/**",
                "C:/Users/oskar/AppData/Local/Arduino15/packages/sparkfun/**",
                "C:/Users/oskar/AppData/Local/Arduino15/packages/SparkFun/hardware/apollo3/2.2.1/cores/arduino/mbed-bridge/core-api/api/deprecated-avr-comp/avr/**",
                "C:/Users/oskar/AppData/Local/Arduino15/**",
                "C:/Users/oskar/Documents/Arduino/libraries **"
            ],
            "browse": {
                "path": [
                    "${workspaceFolder}",
                    "C:/Users/oskar/Documents/Arduino/libraries/**",
                    "C:/Users/oskar/AppData/Local/Arduino15/packages/esp32/**",
                    "C:/Users/oskar/AppData/Local/Arduino15/packages/arduino/**",
                    "C:/Users/oskar/AppData/Local/Arduino15/packages/sparkfun/**",
                    "C:/Users/oskar/AppData/Local/Arduino15/**"
                ],
                "limitSymbolsToIncludedHeaders": true,
                "databaseFilename": ""
            },

            "forcedInclude": [
                "C:/Users/oskar/AppData/Local/Arduino15/packages/esp32/hardware/esp32/3.0.3/libraries/Wire/src/Wire.h",
                "C:/Users/oskar/AppData/Local/Arduino15/packages/esp32/tools/esp-rv32/2302/lib/gcc/riscv32-esp-elf/12.2.0/include-fixed/limits.h"
            ],
            "cStandard": "c17",
            "cppStandard": "gnu++17",
            "defines": [
                "USBCON",
                "_DEBUG",
                "UNICODE",
                "_UNICODE",
                "ARDUINO=10812"
            ]
        },
## WiFi

To the right you can see the webpage which is used to controll the glider when it is at the surface.
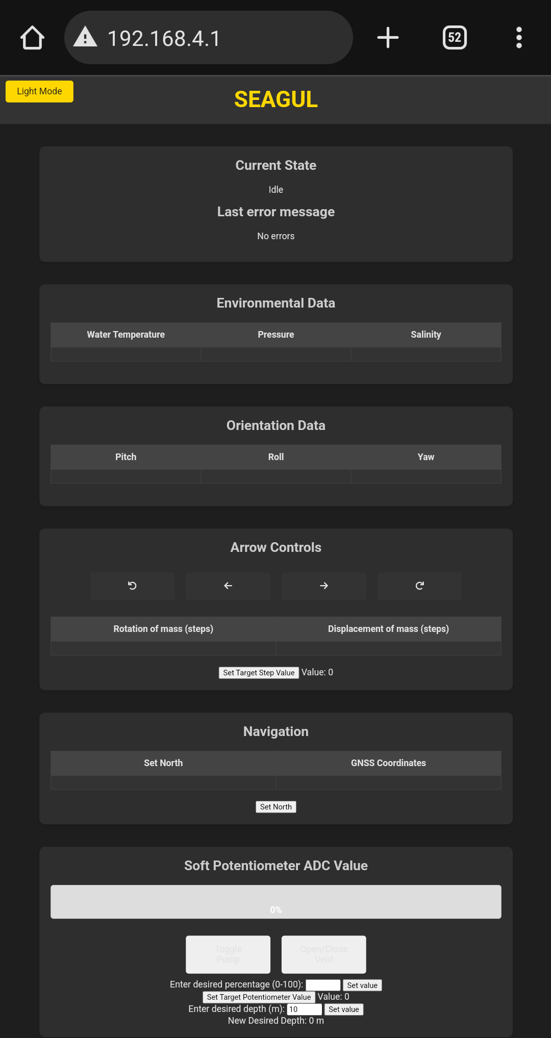
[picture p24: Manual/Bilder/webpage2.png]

 The website showcases sensor values, potentiometer value, ballast possition and allows the glider to enter some states. 

The Webpage is also useful when testing the glider in the lab, as you can make sure that the proper values are being read and all of the glider can be controlled. 

When starting the glider the ESP32 will sit in the init state. Before you are able to controll annything you have to enter the IDLE case with the button near the bottom of the webpage. You can always make sure that the right case is entered by the 'error message' and 'Current state' at the top of the page.

***Error message doesn't indicate and issue, it is merely the latest message sent from the ESP32.***

Before initiating a dive, make sure that you have set a target possition for both the potentiometer and the steppermotors. You also have to set a desired depth. 

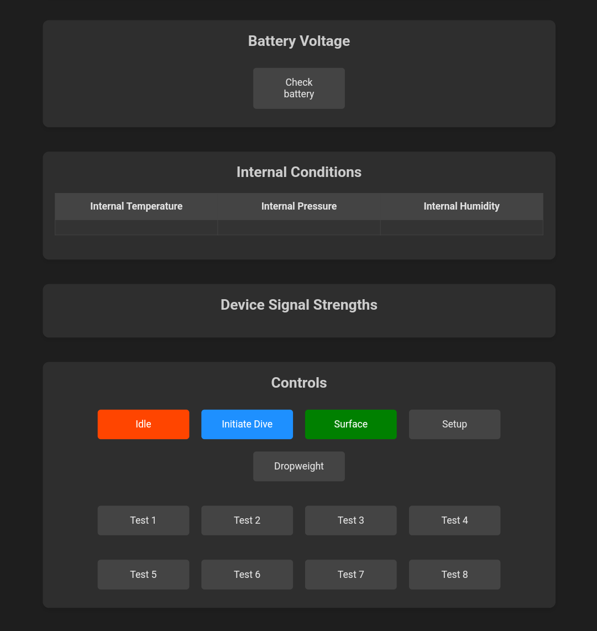
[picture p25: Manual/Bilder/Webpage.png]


It is important to note that the Wifi signal dissapears as soon as more the half the glider is submerged. 

To reach the website you need to connect to the Seagul network, which is available as soon as the ESP32 is running.
The password is **0123456789**. When connected, open a browser and enter **192.168.4.1** in the search field.
<br clear = "right">

## Electronics

## Useful knowledge
Bellow follows some important general knowledge about the glider.

- The steppermotors can be configured for microstepping (see [2. Electronics](2.%20Electronics.md)). In the gliders current state the microstepping is set to 1/16 which allows for smooth motion and precise movement. When utilising the max range on the translaitonal movement, the values therefore go from 0 - 6200\*16 = 0 - 92000 steps. The rotaitional motors go \+/\- 250\*16 steps.

- The value for the fullness of the oil reservoir on the webpage doesnt display the fullness in percent, but rather the potentiometers min and max value as a percentage. At the moment the external bladder is empty at ~2600 and empty at ~1700. 

- When controlling the glider from the webpage before start, several things are needed. Always start with putting the glider in **idle**. Make sure to **set a target value** for both the potentiometer and the translational motor. Make sure to set a **max depth** for the glider.

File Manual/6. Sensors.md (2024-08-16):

# Sensors

## Atlas conductivity sensor
Länk till kalibrering och användning av konduktivitetssensor (Atlas Scientific) med I2C och UART https://how2electronics.com/interfacing-atlas-scientific-ph-sensor-with-arduino-via-uart-i2c/
### Calibration data

The following strings are exported after a calibration of the conductivity sensor on August 5, 2024. The calibration is a three-point calibration, where the first point is dry calibration, then low calibration with 18,880 $\mu S$ and high calibration with 80 000 $\mu S$.

1. BA3806430000

2. 803F312E3000

3. 00FF713D0A3F

4. 01F4FEFF64F6

5. FCFF77240300

6. 6E8016000040

7. 9C47DCAC0B00

8. C25F12000040

9. 494601010201

10. 00010000E5B7

These can be used to import to a new conductivity sensor or in case the calibration has disappeared for some reason.

## Orientation sensor (IMU)

Länk till instruktioner för kalibrering av [magnetometer](https://thecavepearlproject.org/2015/05/22/calibrating-any-compass-or-accelerometer-for-arduino/). Before calibrating the orientation sensor we highly recommend you discuss with Krister Blanch as he has a lot of experience regarding IMU and will probably be happy to help!

## Temperature sensor

## Pressure sensor

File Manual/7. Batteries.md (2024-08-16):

# Batteries

The batteries are bought from MaxAmps and are Lithium Ion 9S 32,4 V battery packs. For more information read on their product page:
https://maxamps.com/collections/9s-32-4v-li-ion/products/li-ion-10350-9s3p-32-4v-battery-pack

## Storage

The batteries as well as the charger are stored in a black tin cabinet. Having the batteries next to each other is not really optimal, new storage options should possibly be investigated. 

If the batteries are going to be stored for a longer period without being used it is a good idea to first discharge them. The charger has a discharging feature.

## Charging routines

Li-ion batteries needs to be handled with care and caution since battery fires can be extremely problematic and dangerous. It is therefore very important to follow safe procedures when it comes to charging. 

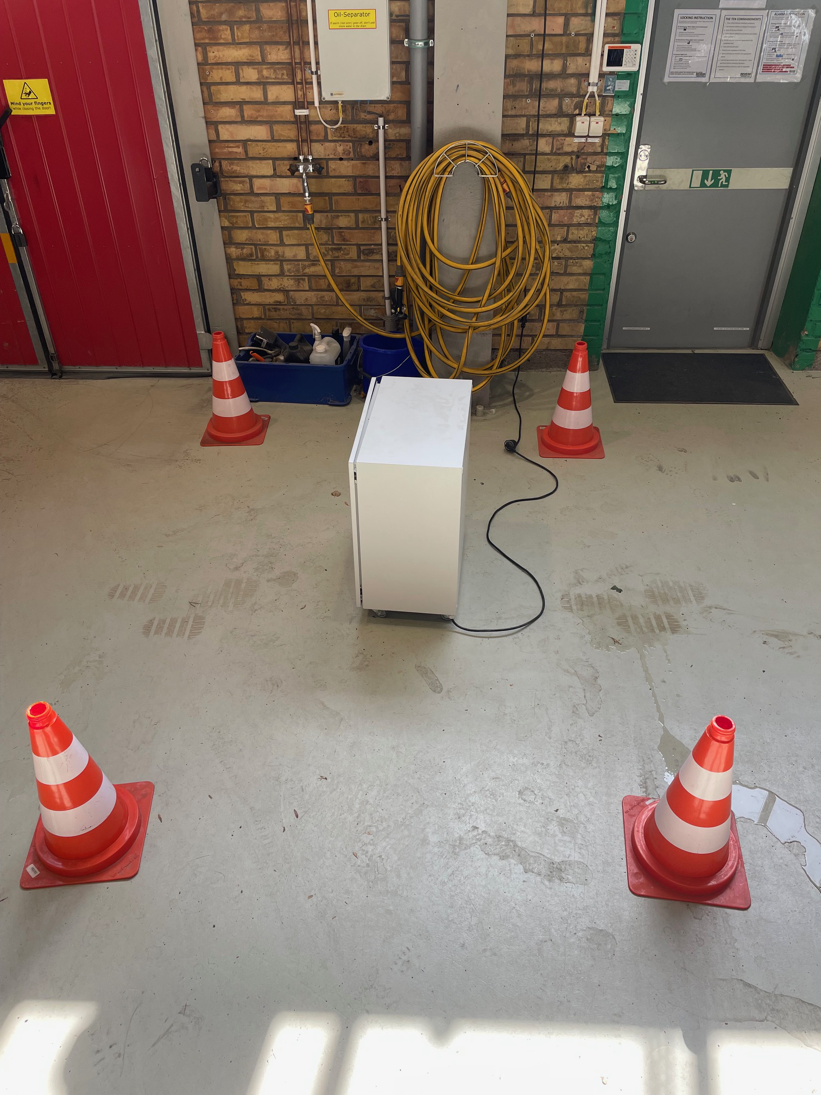
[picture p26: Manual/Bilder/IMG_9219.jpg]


Firstly, the area used when charging should have easy access to the outdoors so that the cabinet can easily be moved outside in case of fire or other emergency. It is also extremely important that the charging area does not block any emergency exits. A good example of area for charging is close to the big gate in Revere (make sure to unlock the doors and place cones before starting). 
<br clear="right"/>

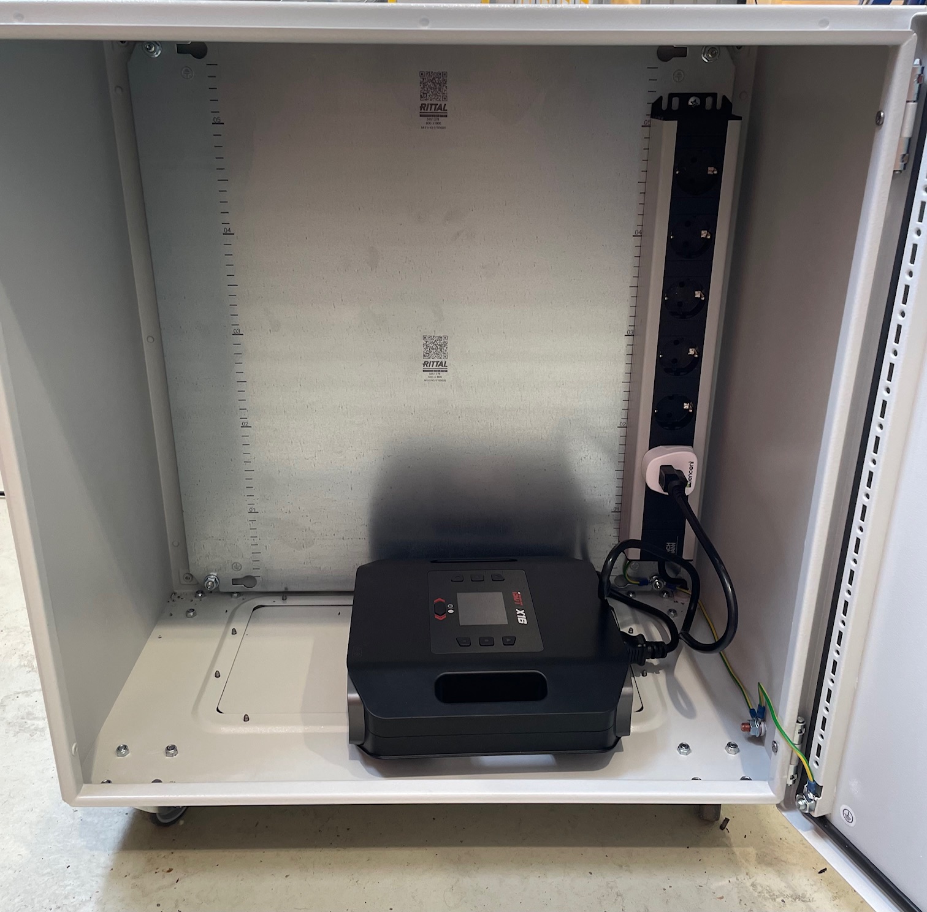
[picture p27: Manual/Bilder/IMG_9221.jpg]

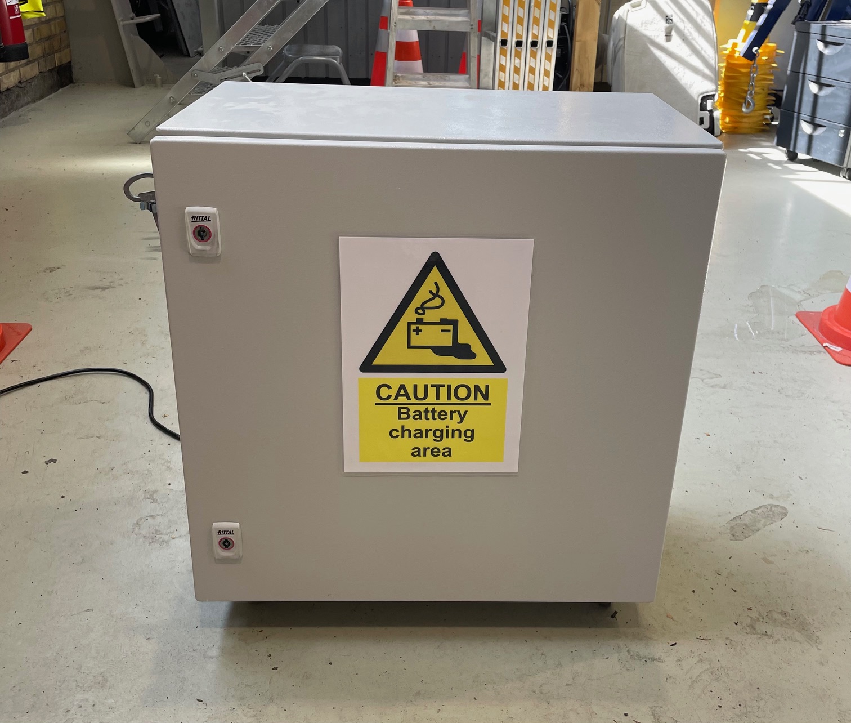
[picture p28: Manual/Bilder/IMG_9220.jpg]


Charging should always take place in the designated cabinet. 

Connect the charger to the outlet inside the cabinet and turn it on by pressing the power button.
<br clear="right"/>

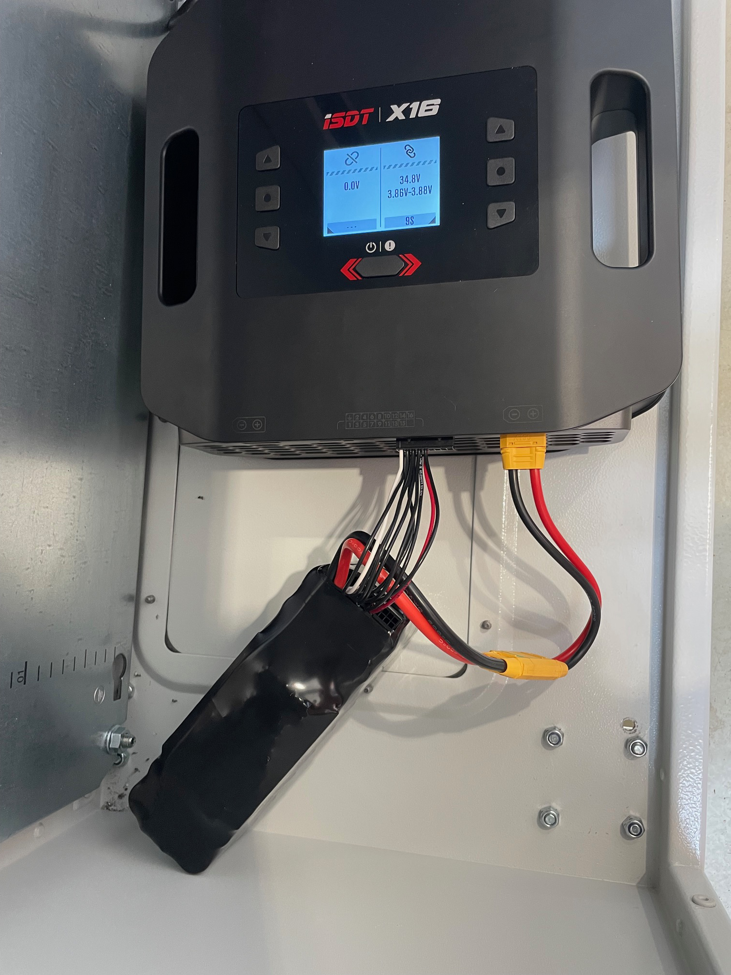
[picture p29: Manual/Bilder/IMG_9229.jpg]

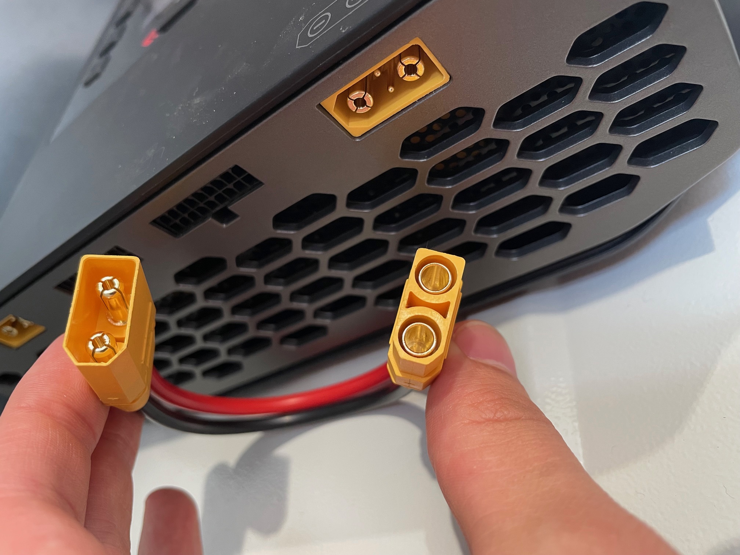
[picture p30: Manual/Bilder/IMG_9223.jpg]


Connect the battery to the charger by first plugging in the balancing lead. You may notice that the xt90 antispark connector from the battery does not fit directly into the charger since the outlet has two extra pins (xt90i). The extra pins aren't necessarily needed so we can use an adapter cable as shown in the picture to the left. The manufacturer, MaxAmps, has confirmed that this is ok to do.
<br clear="left"/>

Once the battery is correctly connected to the charger, you should be able to see the voltage status of the battery and the different cells. 

In order to start charging: 

- Press and hold the circle-button (the one between up and down arrows)
- Scroll down and press "Custom Task"
- Chemistry: LiPo (this is ok since Li-ion can handle more voltage than LiPo)
- Task: Charge
- Current: ~7.5 A (it is recommended to use 0.5C - 1C while charging. 10.35 A corresponds to 1C and would take one hour to fully charge the battery)
- Cells: 9S
- Condition: 4.20 V
- Press "Start"

**!!! Always keep the battery attended during charging. If the battery becomes abnormally hot, stop charging immediately and place the cabinet outside. !!!**

In order to stop charging:

- Press and hold the circle-button
- Press "Stop"
- Turn off the charger by holding the power button
- Disconnect battery cables

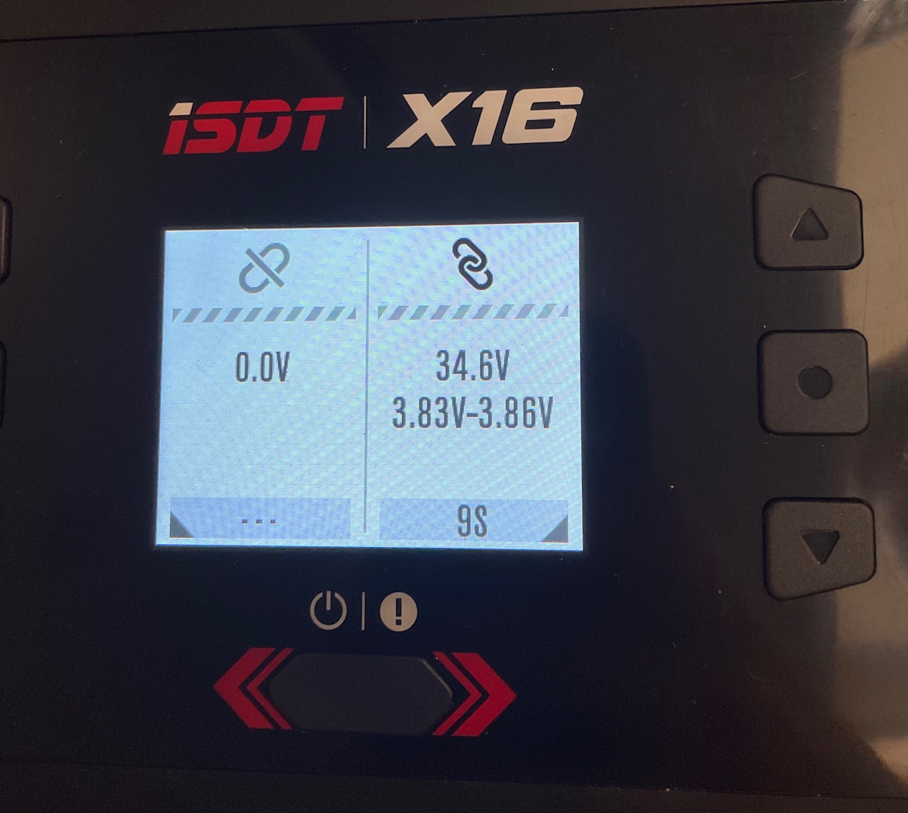
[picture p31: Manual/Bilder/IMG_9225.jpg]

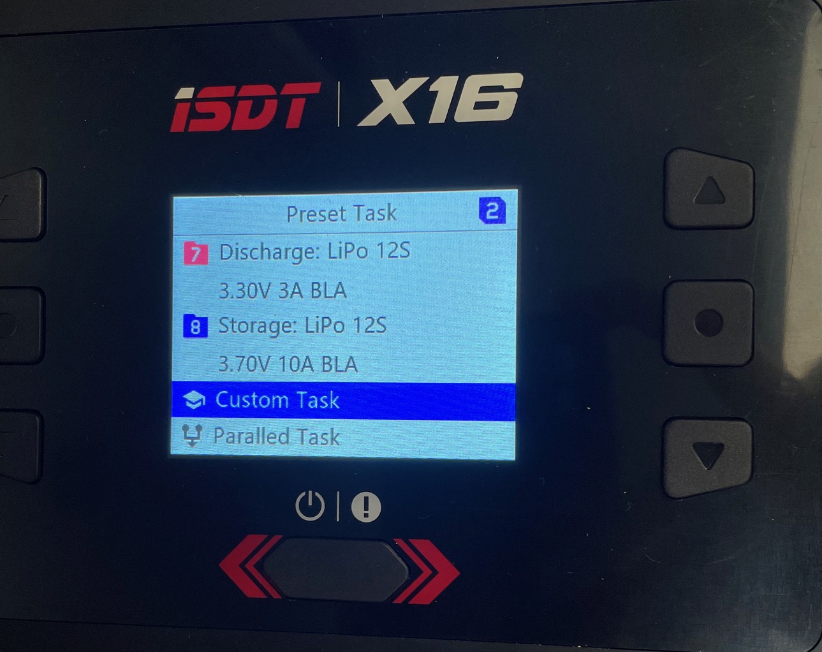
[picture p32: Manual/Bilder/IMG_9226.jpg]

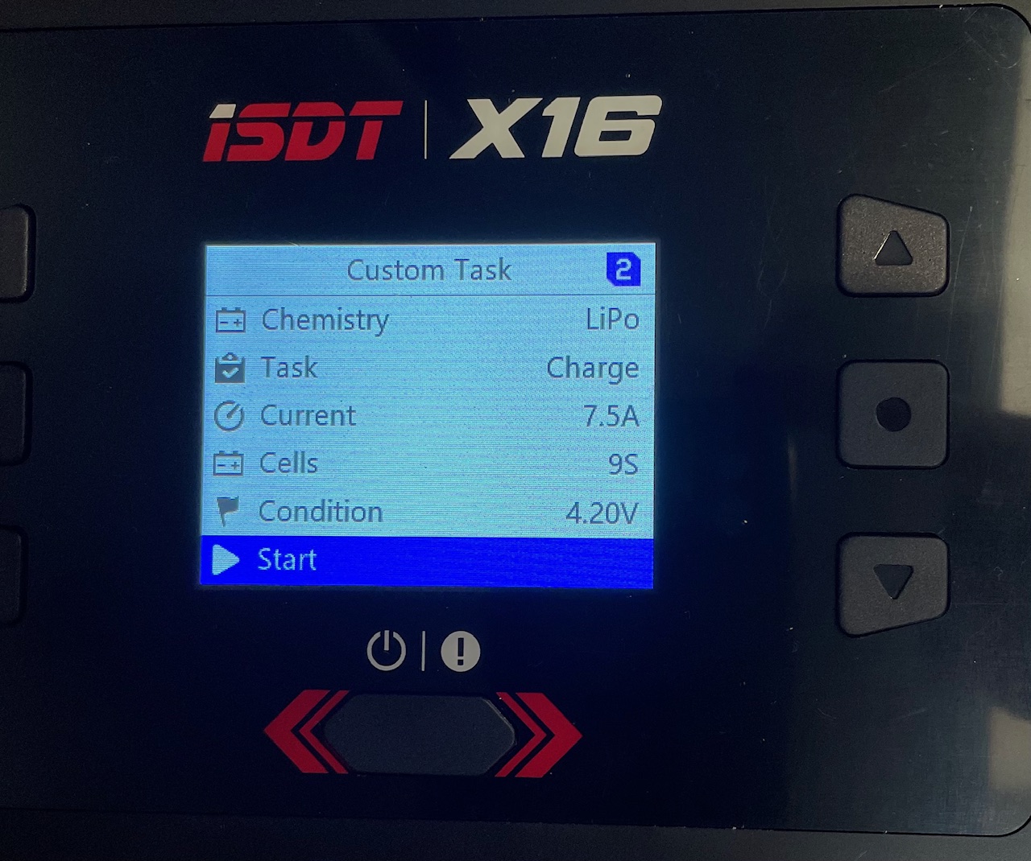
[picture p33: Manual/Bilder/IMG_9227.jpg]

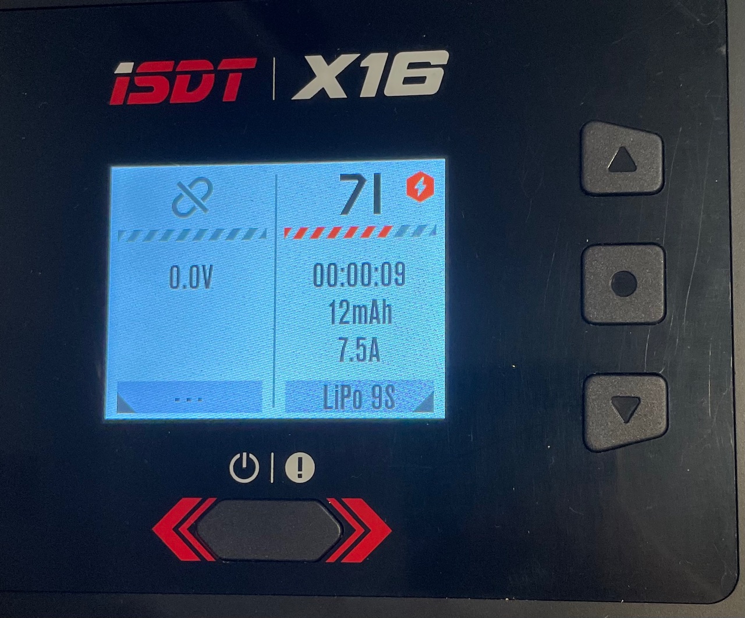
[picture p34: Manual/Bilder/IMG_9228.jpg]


<br clear="left"/>

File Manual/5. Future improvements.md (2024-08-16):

# List over future improvements

* Make the planetary gear in metal (beware of weight distribution in the glider)
* Bushing for the weight package in the manouvering module
* Investigate potential leak in the pump module
* Print new parts in PETG (PLA deteriorates in saltwater)
* Remake manouvering module (can be shorter with a smarter design)
* Electrogalvanize the dropweights instead of using zinc spray
* New Grayhill 30-3ul switch connected to control system and dropweight
* Parallel connection of two batteries (ideal diode circuit with load switch function)
* Configure software to be able to measure battery level during use

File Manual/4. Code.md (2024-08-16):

# Code
The following section will serve as an overview of the exisitng code and the main thought process behind the decisions. The most recent versions of the code can be found in **AGT_6** and **glider6** in the folder ***Huvudprogram***.

## ESP32
The structure for the code is built upon two main chracteristics. Firstly the ESP32S3 has a dualcore processor, which enables it to split the code into two separe tasks that can be run simultaniously. This is done through the **void glidercontrol** and **void datagathering** whichs allows the glider to steer and collect data at the same time. Secondly the **glidercontrol** is split into cases which allows the glider to take different courses of action, depending on its situation. Bellow follows a breif description of the code structure:

- **includes, defines, variables** these make up the global variables and booleans aswell as libraries and definitions of pins.
- **voidHandles**, these are functions for the webpage.
- **voids**, these are functions for the glider.
- **void glidercontrol**, this is the running code for the glider. It contains a case structure which decides what actions are being taken. This void is run on one of the two cores.
    - **Gliderstate switch**
        - **Glider_init** is the initialization of the glider and its sensors.
        - **idle** is the resting state of the glider. From here it is meant to be controlled from the webpage.
        - **diving** is the start of the dive, the bladder is being emptied.
        - **gliding down**, this is where the glider exists when it is sinking. When the bladder is empty, the stepper motors begin too move. Then the glider waits for the right depth.
        - **gliding up** enters when the right depth is reached, the bladder begins filling and when full, the stepper motors puts the ballast package into place.
        - **Surface** is the state for when the glider is at the surface and decides what to do next. 
        - **Dropweight** is entered when the ESP32 has released the dropweight.
- **void Datagathering**, this runs in the background during normal operation of the glider. It constantly reads values from all the sensor and stores them in 'bunches' on the SD card.

### Notes on the current state of the code
At the moment the glider has rudementary functions for the most part, with huge room for improvement.

***Gliding down/up:***
At the moment, the only thing happening in these cases are the bladder filling/emptying and the steppermotors moving the ballast. There is room to in a more intriquite way incorporate regulation of the ballast positions for both roll and translational movement. 

***Surface***
This is mostly unfinnished, at the moment the code is built to simply get in a state of wifi controll. Although in the later parts of the code (maybe as comments) is the beggining of a communication system with the AGT. Not all cases are added to this yet, but the main logic is there. 

***General***
All throughout the code there are improvements that can be made regarding security and efficiency. This is talked more about in 5. Future Improvements. The main issues here are implementations of battery measurements and handling of the dropweight case. 

### Webpage
The code for the webpage is handled through the page.h file. Here the layout is written in **HTML** code and the functions in **javascript**. The interactions with the ESP32 are made through the **voidHandle** funcitons and and the **server.on** commands in void setup(). 

## AGT 

The code for the AGT is built on case structures and interactions with the ESP32. The part of the code which handles the satelite and GPS communication is based on the Sparkfun AGT repsitory nad their 'simple tracker and better tracker' examples. Additionally code has been implemented for communication with the ESP32 and release of the dropweight in case of emergency.

- **includes, defines, variables** these make up the global variables and booleans aswell as libraries and definitions of pins.

- **voids**, these are functions for the AGT.
- **void loop**, this is the running code for the AGT. It contains a case structure which decides what actions are being taken.
    - **State switch (loop step)**
        - **Loop_init** is the initialization of the AGT and decides what to do when woken up.
        - **Pickup** is the case when the glider is at the surface and periodically transmits its possition.
        - **Read UART** is when the AGT and ESP32 are communicating
        - **zzz**, this is where the sleeping case for the AGT when the glider is submerged.
        - **Wakeup** wakes up.
- **Functions for translating messages**

### Notes on the current state of the code
The code works in its current state. On the ESP side there arn't cases corresponding to all cases in the READ_UART loop step. Furthermore some timeout and sleep time parameters may need some adjusting. 

***General***
Many of the code segments regaridng the modem are very sequential. Since the AGT uses the same antenna for the Iridium and GPS, only one works at a time through the RF-Switch. Therefore the AGT needs to power up and power down one function at a time to not damage any components. 

When writing the code, keep in mind that some 'problems' that VScode finds, can't seem to be resolved. When analysing the code, expect ~70 problems. The code should however always analyze and verify correctly before uploading. 

Also when analyzing, makesure to have the correct board configured in VScode, otherwise it won't analyze correctly.

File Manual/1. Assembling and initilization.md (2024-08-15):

# Assembling the glider

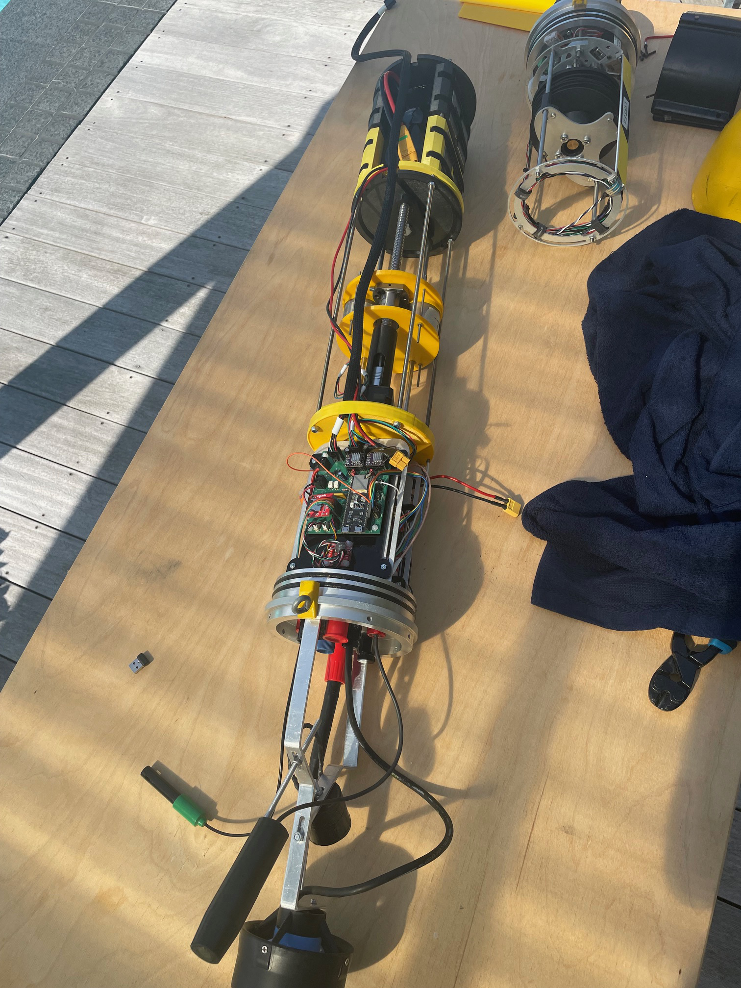
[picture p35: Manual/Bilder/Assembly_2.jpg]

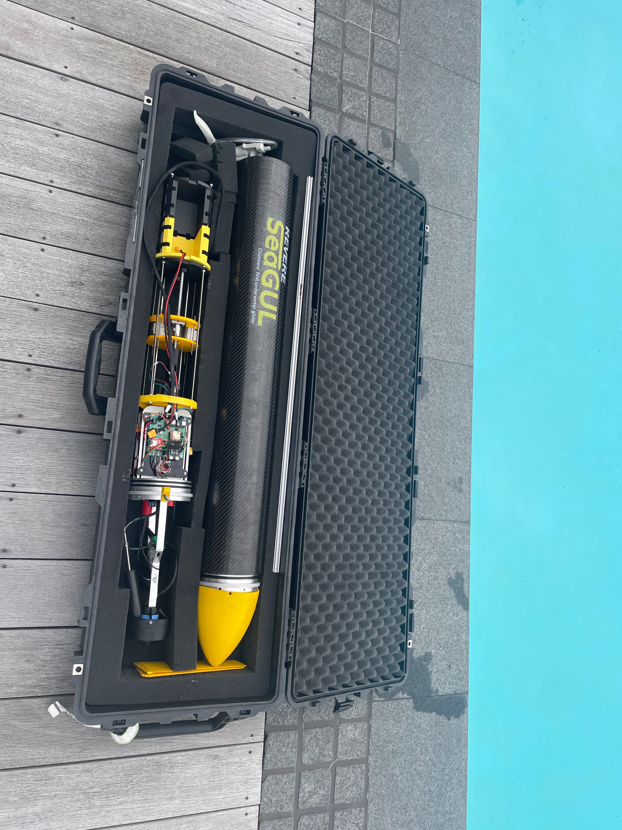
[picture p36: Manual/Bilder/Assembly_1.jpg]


When assembling the glider there are several details that are important to be aware of. This file, consisting of images and text, provides a step by step tutorial on how to correctly assemble the glider before use in water. Beware that the procedures can change depending on what changes have been made to the glider since this manual was written.
<br clear="right"/>

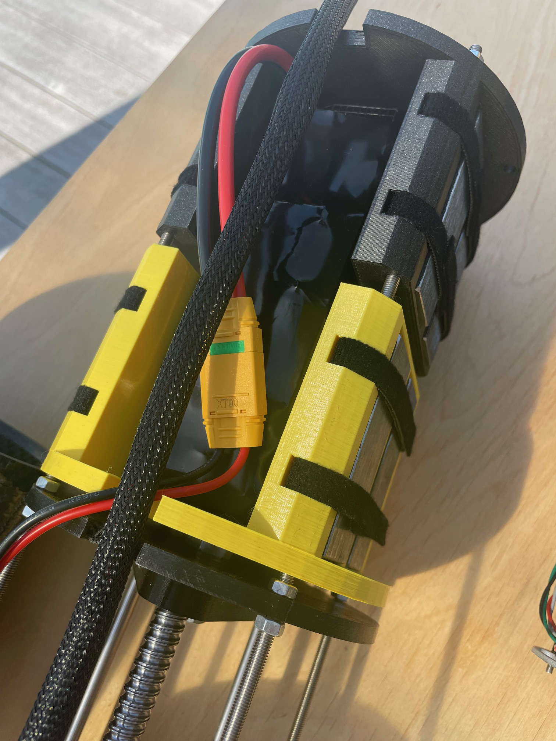
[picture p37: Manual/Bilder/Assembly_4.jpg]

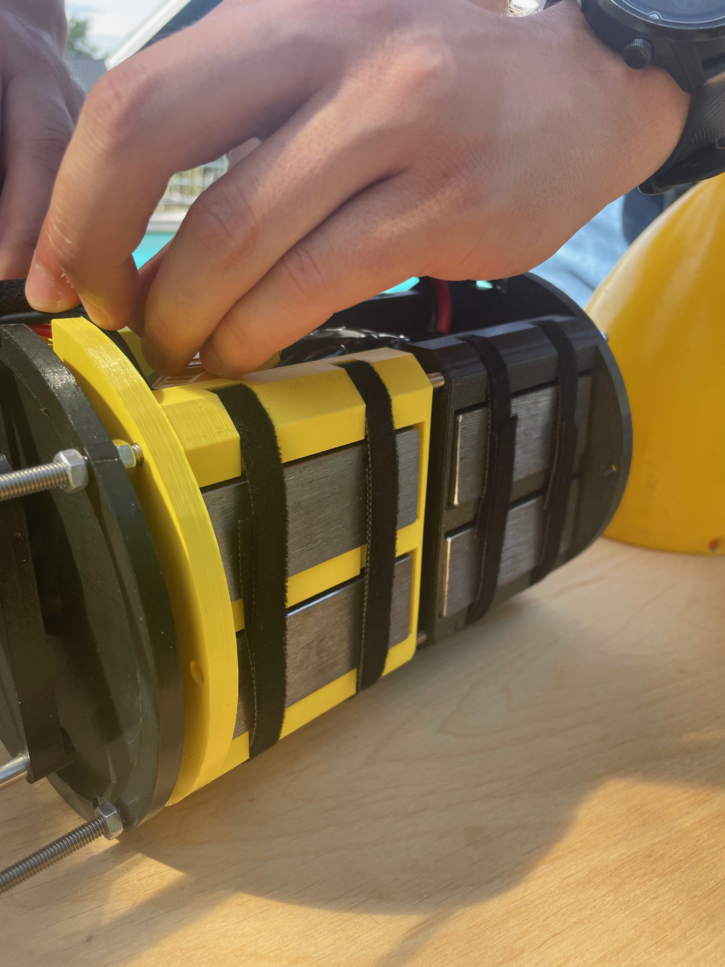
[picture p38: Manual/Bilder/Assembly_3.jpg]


Place the battery in the battery-holder and make sure that the holder is properly ballasted. For example, you might need steel plates under the battery for extra weight. Connect the battery to xt90 cable running across the module.
<br clear="right"/>

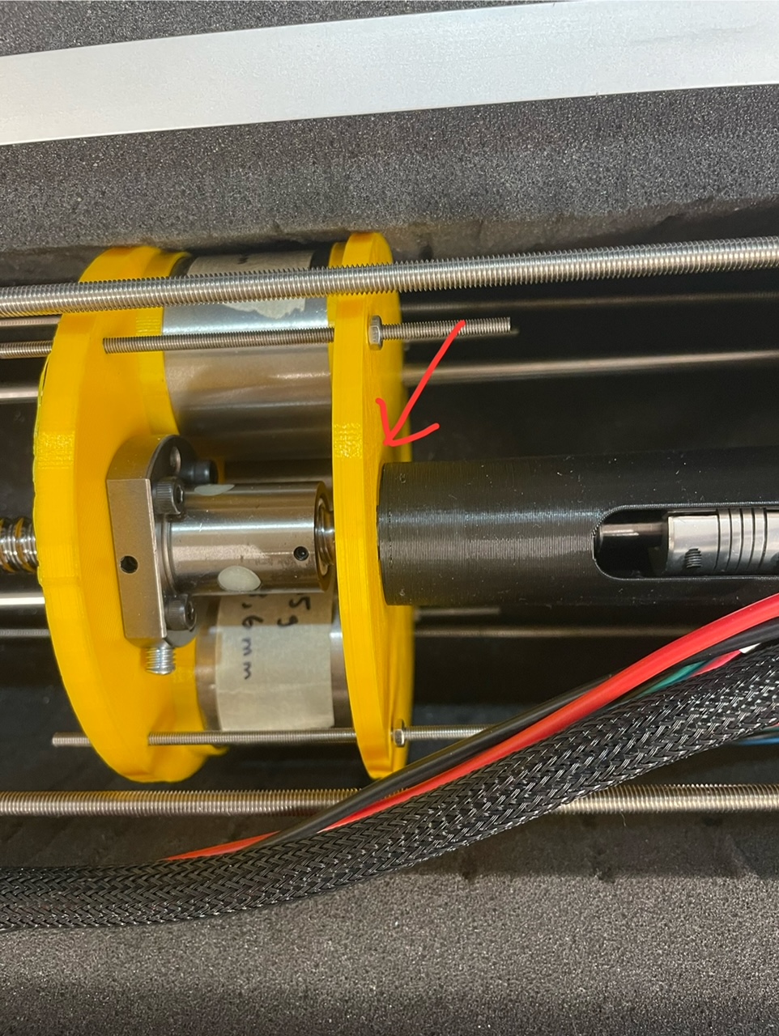
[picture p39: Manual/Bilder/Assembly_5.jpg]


Move the weight package by twisting the ball screw manually. Make sure that the weight package aligns with the end of the black cylinder as illustrated in the picture to the right. This will be position 0 for the translatational stepper motor and you will not be able to move the weights further back than this position during dives. 
<br clear="right"/>

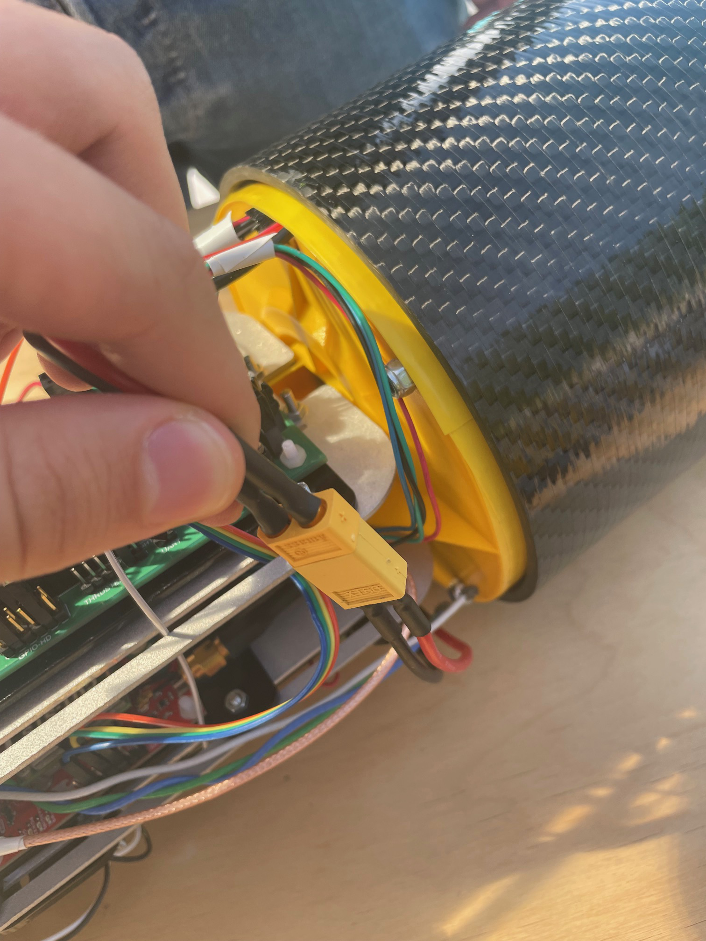
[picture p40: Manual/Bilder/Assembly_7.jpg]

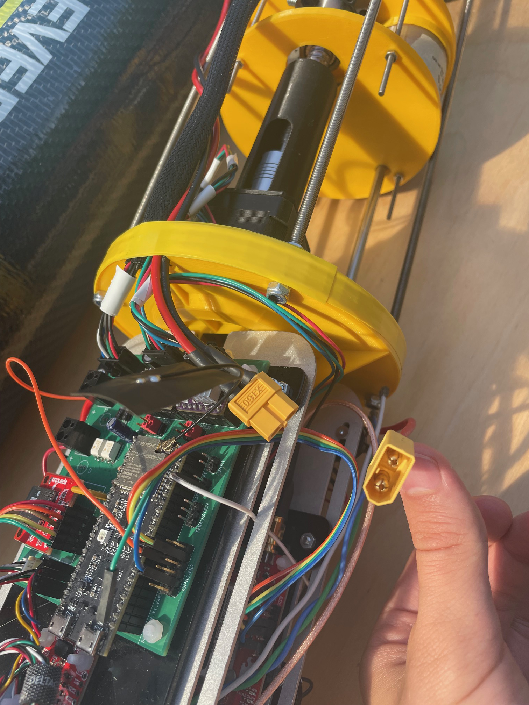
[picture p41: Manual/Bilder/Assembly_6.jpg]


Now you can start carefully sliding in the module in the carbon fibre tube. Make sure not to damage the tube or get any cables stuck.

Connect the battery cable to the electronics.
<br clear="right"/>

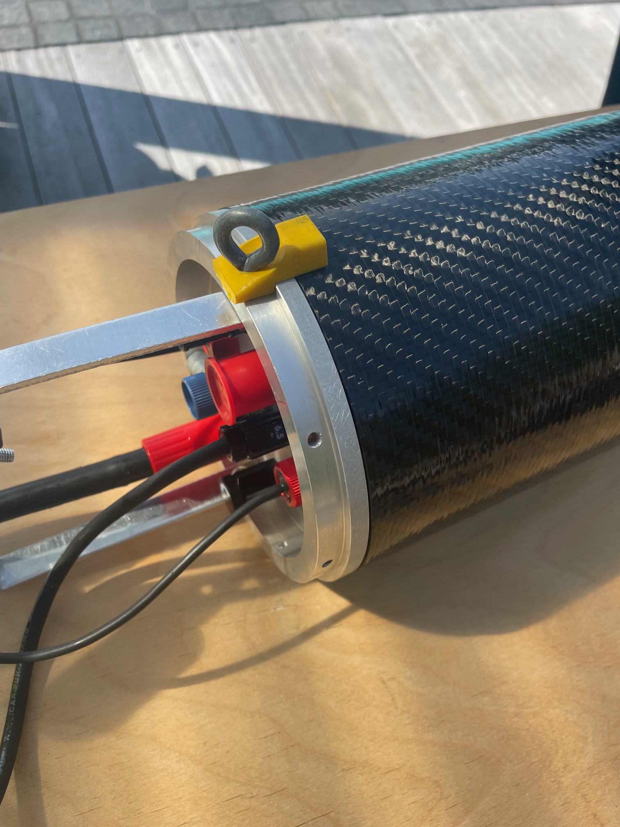
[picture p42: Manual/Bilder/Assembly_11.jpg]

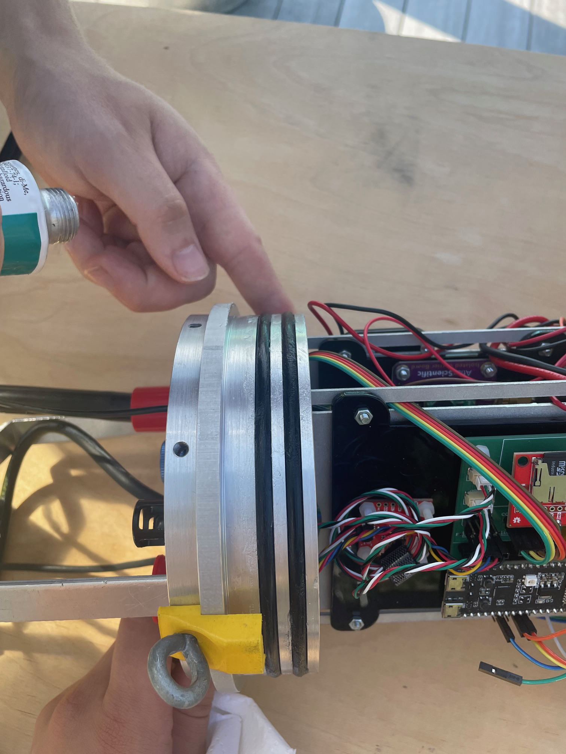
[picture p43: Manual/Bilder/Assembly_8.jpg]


Make sure that the o-rings are properly greased before fully closing the lid. We use Molykote compound 111 that works fine but it might be a good idea to change to compound 55 which is specifically for o-rings since it makes them swell and improves watertightness (they use this at VOTO). 

Damaged or dry o-rings can compromise the watertightness of the glider, especially at higher pressure.
<br clear="right"/>

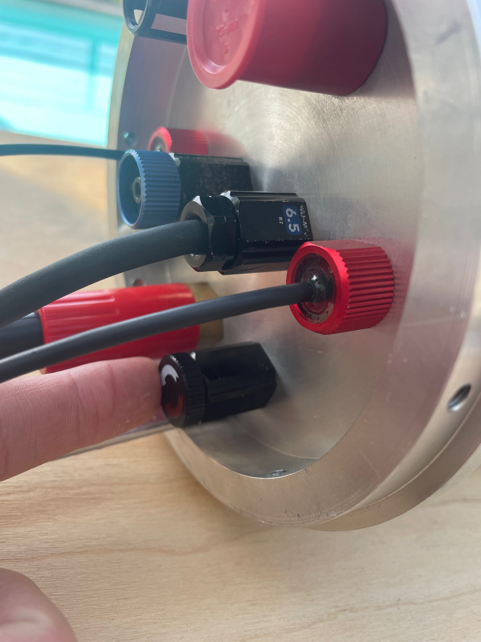
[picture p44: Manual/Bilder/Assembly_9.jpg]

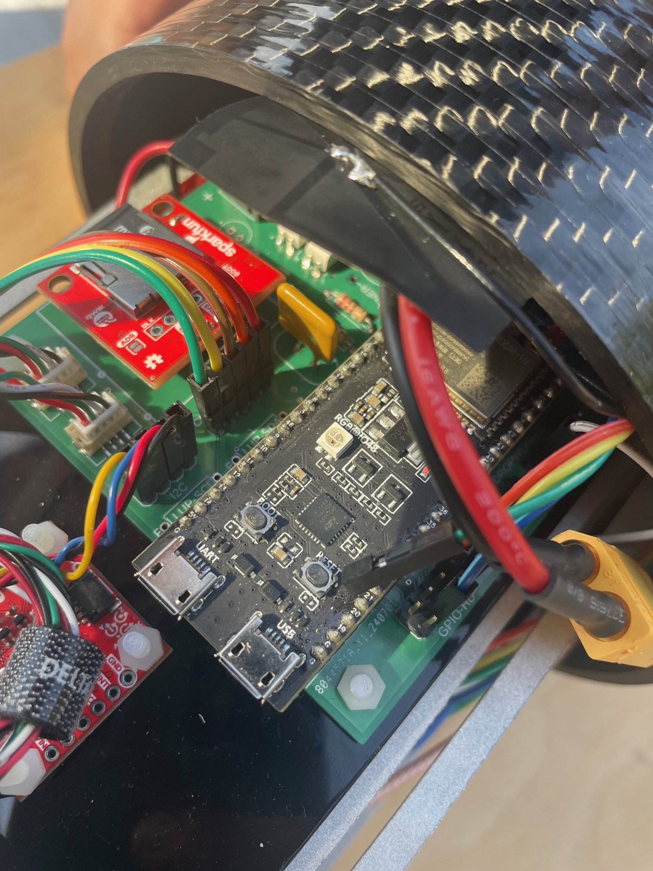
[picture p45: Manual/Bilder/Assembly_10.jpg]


Turn on the electronics by screwing in the power switch from the outside of the rear lid. If you do it before closing the lid, you can press the "reset" button on the ESP32 in order to make sure that the code will be running from the beginning. This is optional since the code should work fine without this step. If you don't decide to press reset on the ESP32 it might be preferable to turn on the power after both lids have been closed.
<br clear="right"/>

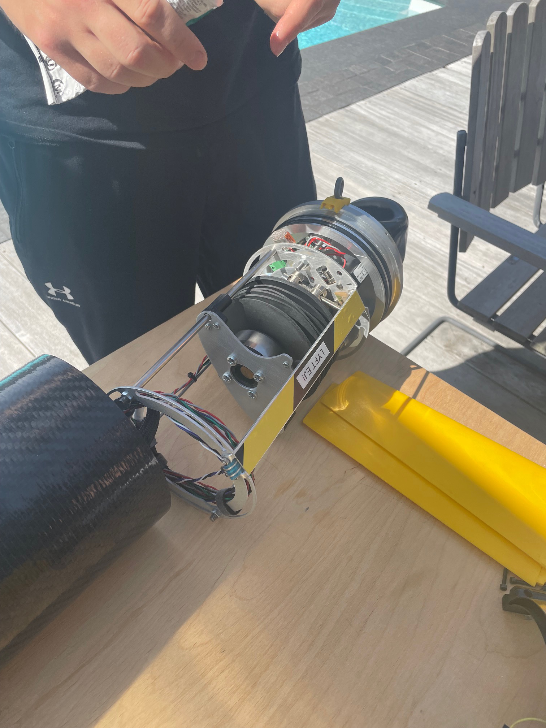
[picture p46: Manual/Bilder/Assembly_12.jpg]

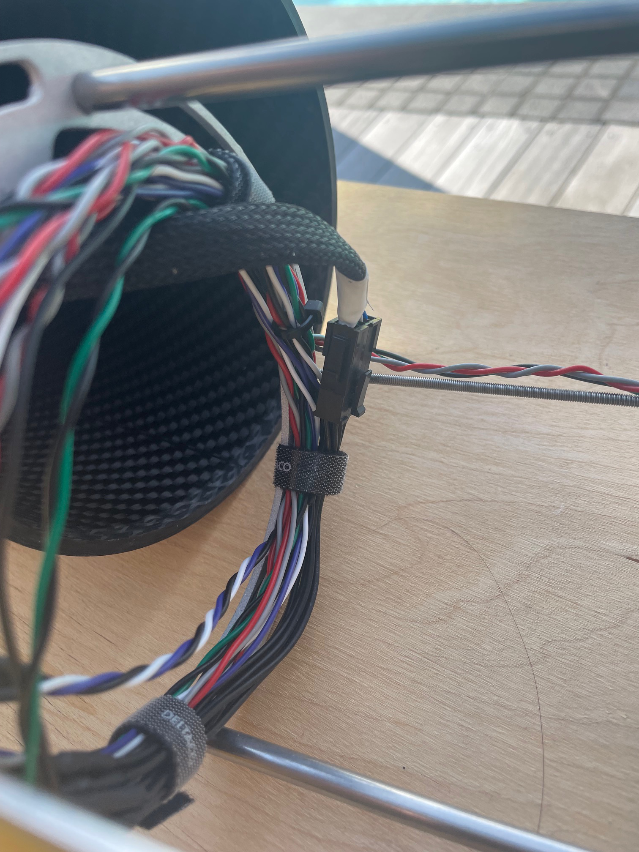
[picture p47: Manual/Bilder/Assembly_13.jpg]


There is a long cable from the electronics that goes through the entire glider, connect this to the pump module.
<br clear="right"/>

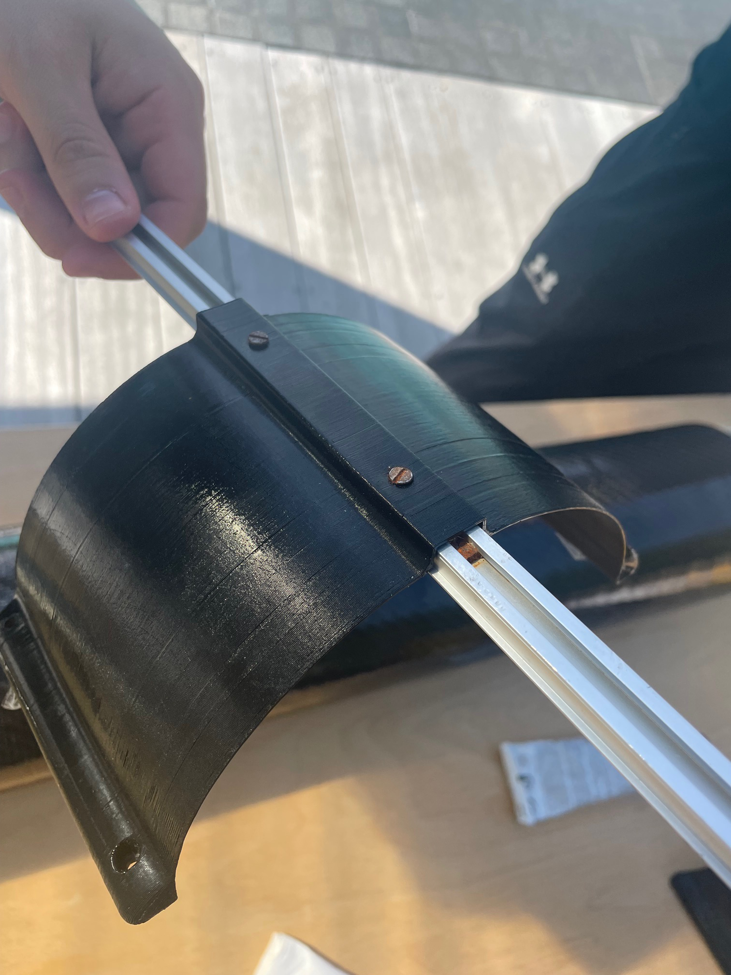
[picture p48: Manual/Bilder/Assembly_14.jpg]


Before inserting the pump module in the tube, make sure that the rail is properly prepared in order to attach the wings later.
<br clear="right"/>

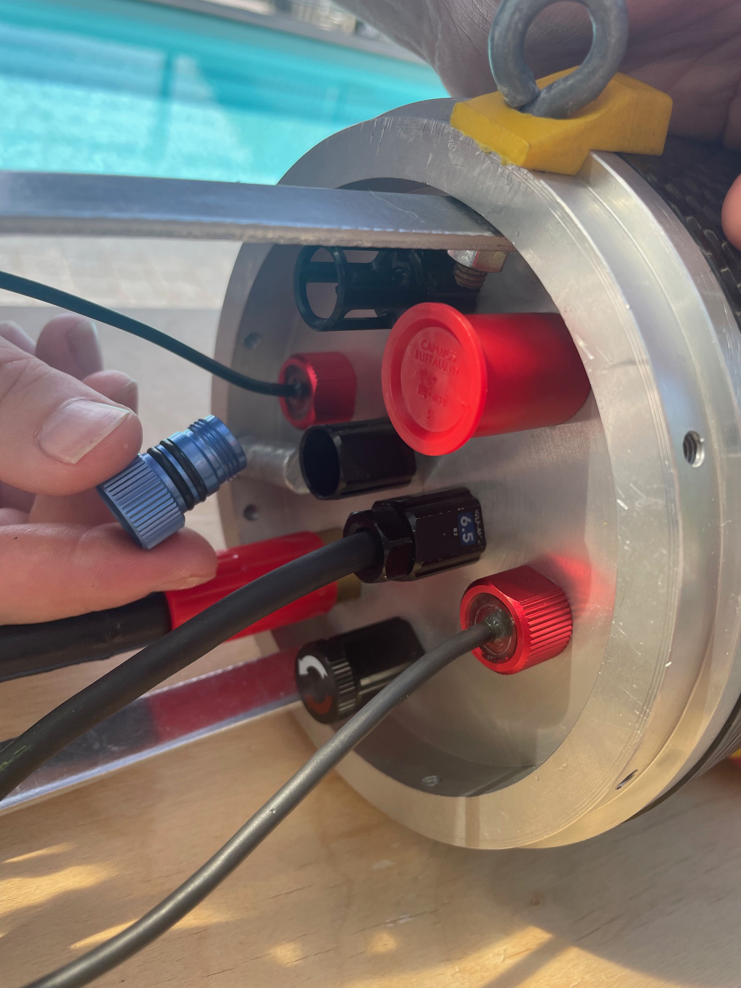
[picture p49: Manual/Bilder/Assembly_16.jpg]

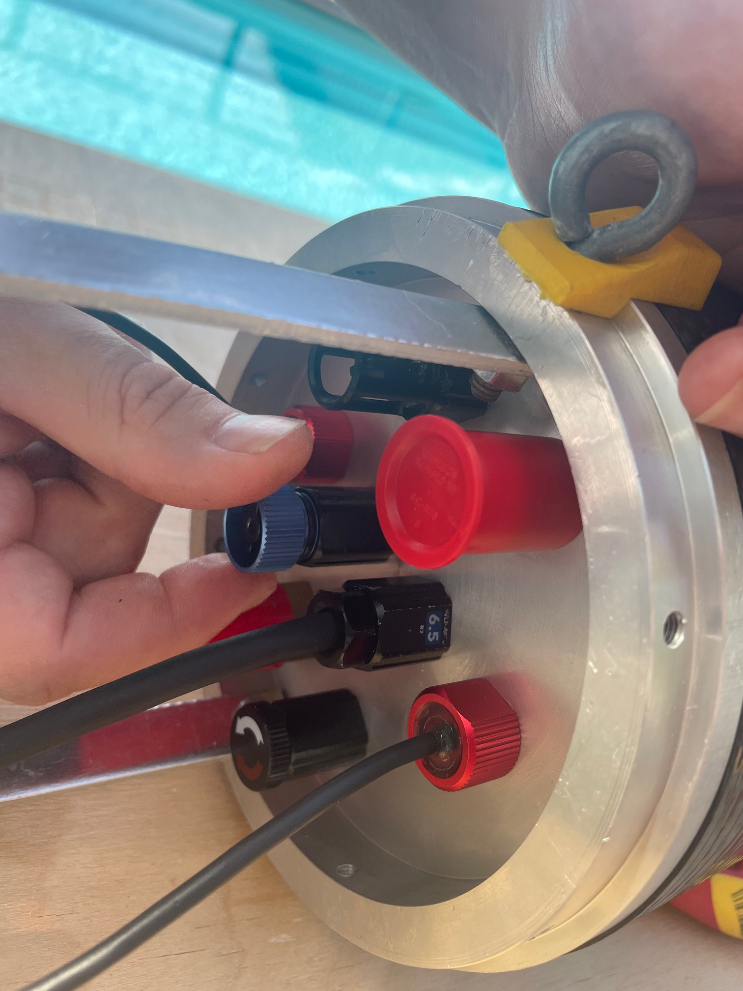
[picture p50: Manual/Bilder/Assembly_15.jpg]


Also make sure to release the pressure valve in the rear lid before inserting the pump module.
<br clear="right"/>

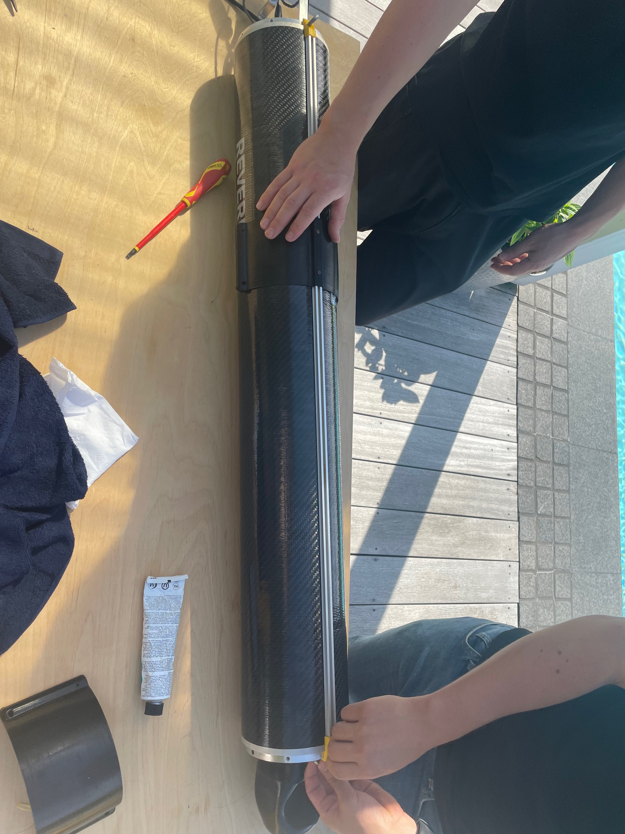
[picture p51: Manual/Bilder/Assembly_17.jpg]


While inserting the pump module it is important that the rail is aligned. You might need to unscrew the "rail-holder" on the front lid before closing it. 
<br clear="right"/>

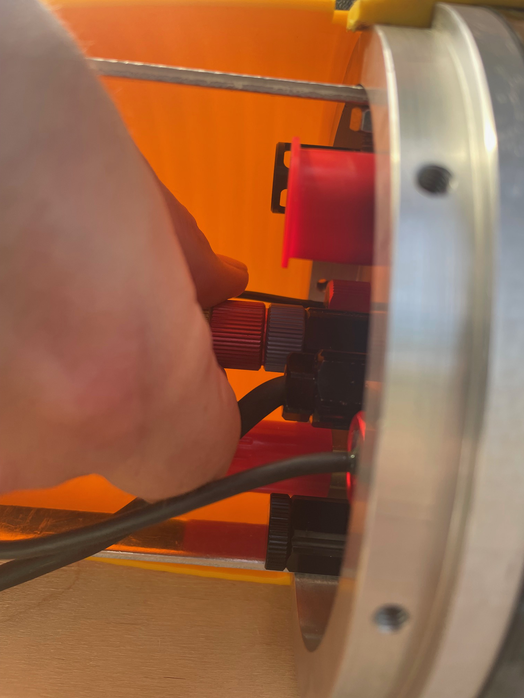
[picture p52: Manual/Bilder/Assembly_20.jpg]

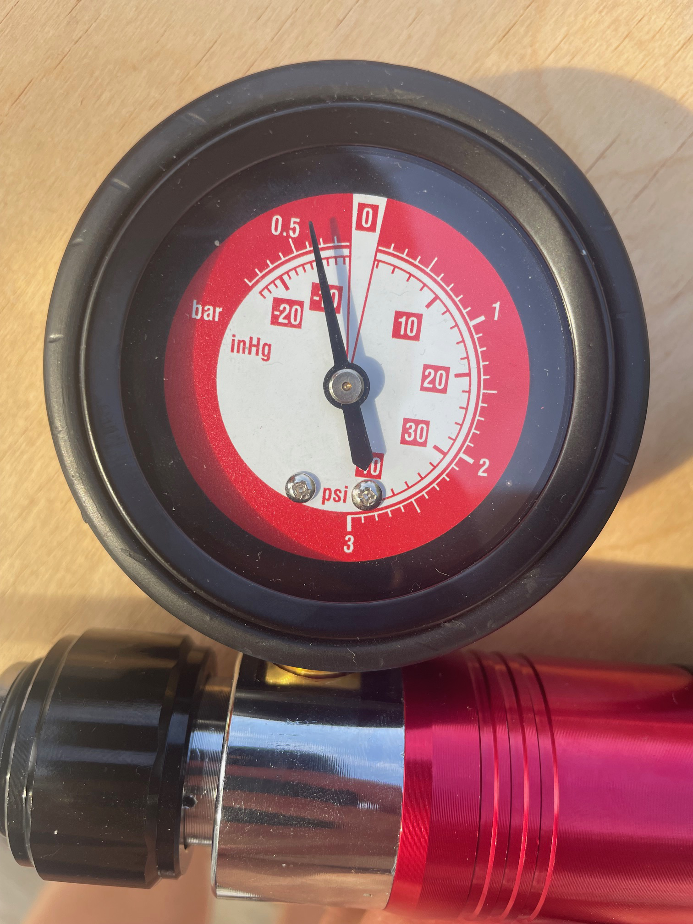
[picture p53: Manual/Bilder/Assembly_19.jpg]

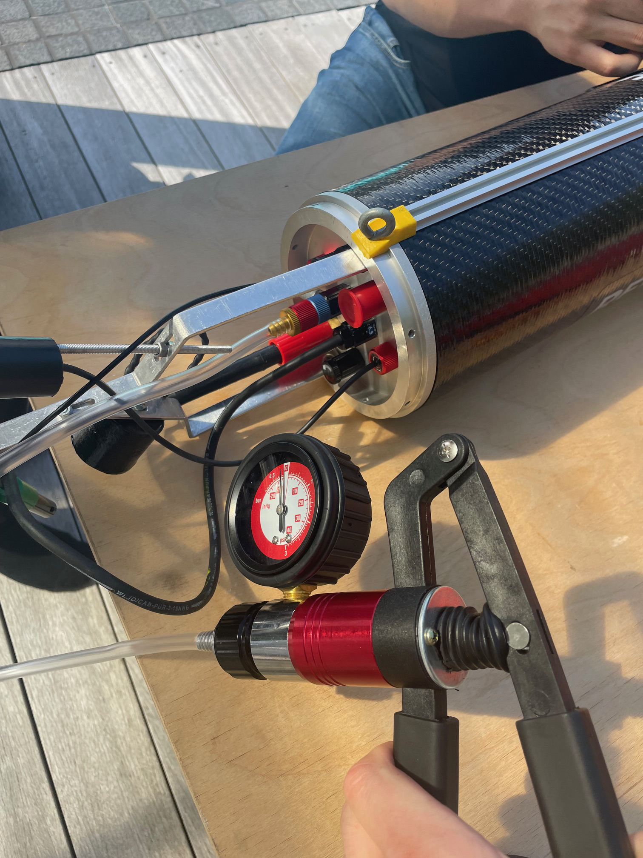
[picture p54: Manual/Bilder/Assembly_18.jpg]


Vacuum pump until 0.7 bar in the glider is reached. This corresponds to 0.3 bar negative pressure (in the picture it is pumped to 0.35 bar negative pressure because the pointer does not start exactly at 0). When unscrewing the vacuum pump be careful that the blue pressure valve stays still and that the red part is fully unscrewed before removed. Otherwise you might release parts of the vacuum and have to start over. The process of pumping takes approximately 12 minutes.
<br clear="right"/>

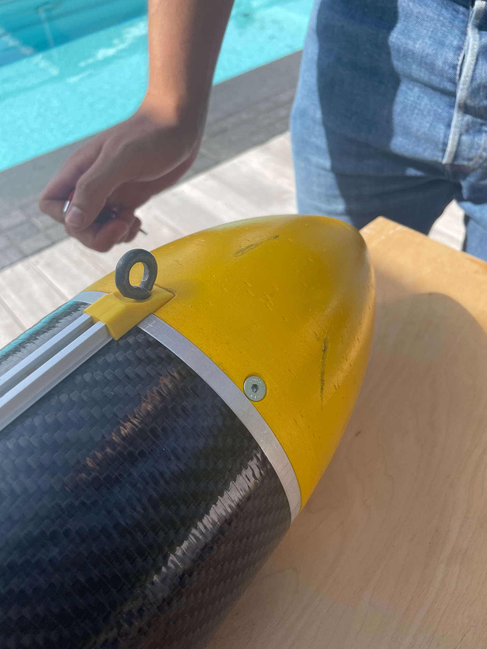
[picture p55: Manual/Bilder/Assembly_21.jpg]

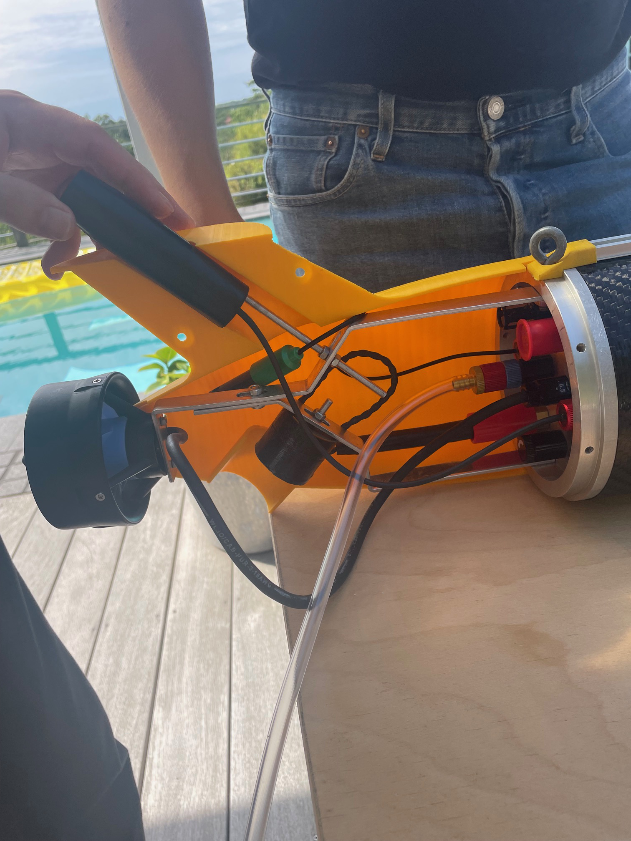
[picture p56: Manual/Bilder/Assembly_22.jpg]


Now it is time to mount the front and rear caps. If available, always use aluminium screws if they are going to be in contact with water. If two different types of metals are in contact under water (especially salt water) there will be corrosion and the materials will deteriorate.

Remember to remove the protective cap from the pressure sensor and make sure that there are sacrificial anodes on both front and rear lids.
<br clear="right"/>

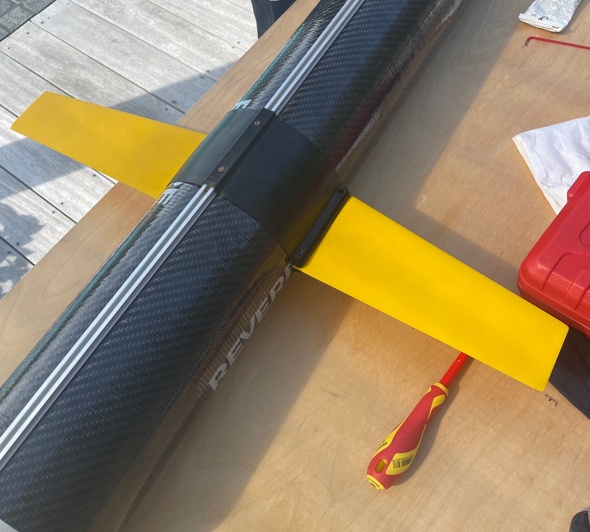
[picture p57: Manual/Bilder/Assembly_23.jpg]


Mount the wings by clamping them between the black "wing holders" connected to the rail. It is a good idea to leave this step until last as the wings reduces mobility of the glider.
<br clear="right"/>

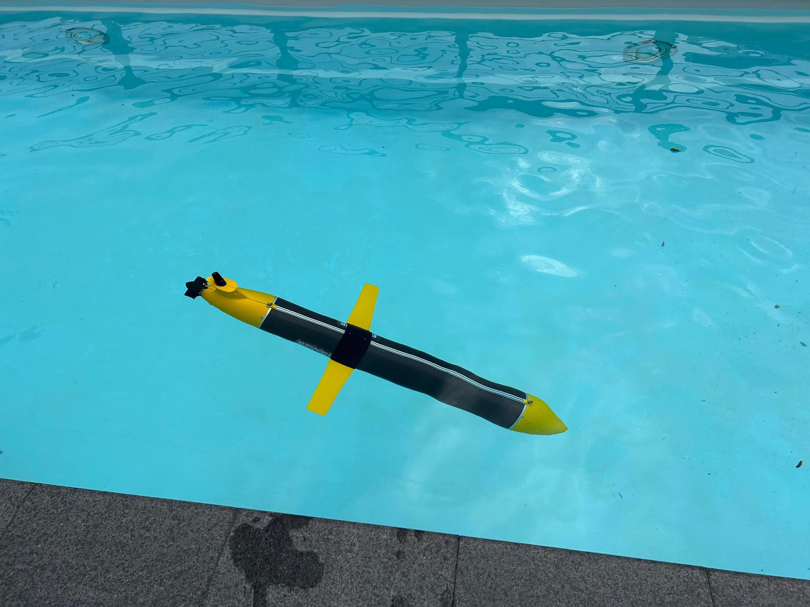
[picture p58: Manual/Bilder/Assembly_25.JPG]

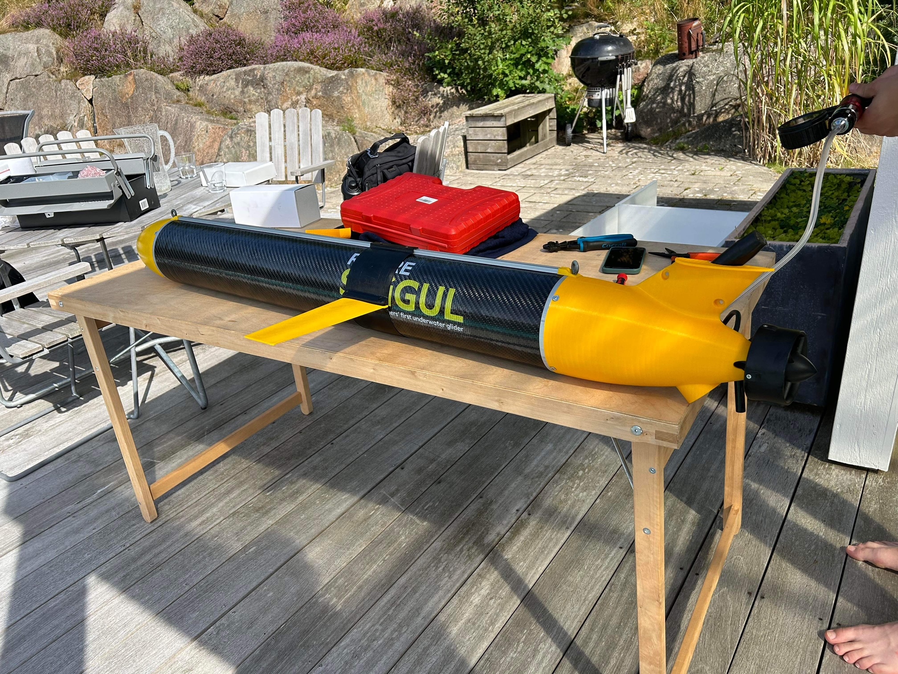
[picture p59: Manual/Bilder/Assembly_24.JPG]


Now the glider is fully assembled and it is ready to be thrown in the water!
<br clear="right"/>

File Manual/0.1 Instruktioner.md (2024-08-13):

# Instructions for further development

## Programming

## Batteries

The batteries are bought from MaxAmps and are Lithium Ion 9S 32,4 V battery packs. For more information read on their product page:
https://maxamps.com/collections/9s-32-4v-li-ion/products/li-ion-10350-9s3p-32-4v-battery-pack

### Charging routines

Li-ion batteries needs to be handled with care and caution since battery fires can be extremely problematic and dangerous. It is therefore very important to follow safe procedures when it comes to charging. 



Firstly, the area used when charging should have easy access to the outdoors so that the cabinet can easily be moved outside in case of fire or other emergency. It is also extremely important that the charging area does not block any emergency exits. A good example of area for charging is close to the big gate in Revere (make sure to unlock the doors and place cones before starting). 
<br clear="right"/>




Charging should always take place in the designated cabinet. 

Connect the charger to the outlet inside the cabinet. And turn it on by pressing the power button.
<br clear="right"/>




Connect the battery to the charger by first plugging in the balancing lead. You may notice that the xt90 antispark connector from the battery does not fit directly into the charger since the outlet has two extra pins (xt90i). The extra pins aren't necessarily needed so we can use an adapter cable as shown in the picture to the left. The manufacturer, MaxAmps, has confirmed that this is ok to do.
<br clear="left"/>

Once the battery is correctly connected to the charger, you should be able to see the voltage status of the battery and the different cells. 

In order to start charging: 

- Press and hold the circle-button (the one between up and down arrows)
- Scroll down and press "Custom Task"
- Chemistry: LiPo (this is ok since Li-ion can handle more voltage than LiPo)
- Task: Charge
- Current: ~7.5 A (it is recommended to use 0.5C - 1C while charging. 10.35 A corresponds to 1C and would take one hour to fully charge the battery)
- Cells: 9S
- Condition: 4.20 V
- Press "Start"

**Always keep the battery attended during charging. If the battery becomes abnormally hot, stop charging immediately and place the cabinet outside.**

In order to stop charging:

- Press and hold the circle-button
- Press "Stop"
- Turn off the charger by holding the power button
- Disconnect battery cables






<br clear="left"/>

## WiFi

## CAD

## Electronics

## Hardware

In 2024, a large part of the mechanical construction and hardware was carried out in collaboration with Pelle Evensen and Henrik Hörlin at FUSE, Chalmers. 

### Rear lid (svarv, genomföringar, radiella hål, skruvar)



A cylinder in aluminum with 150 mm diameter was turned to desired design.
Eight different penetrations were made in the rear lid by first drilling with a 9,8 mm drill. Next, one of the holes was threaded to 7/16 inch to fit a SubConn bulkhead of the same dimensions while the remaining penetrations were reamed up to 10 mm to fit M10 screws.
The penetrations in the rear lid are used for the following purposes:

1. Temperature sensor (M10)
2. Pressure sensor (M10)
3. Salinity sensor (M10)
4. Vacuum valve (M10)
5. Thruster (M10)
6. Antenna (M10)
7. Dropweight (7/16” 20 UNF)
8. On/Off switch (M10)

<br clear="right"/>

In addition, radial holes were drilled in the lid. With 45 degrees of separation, seven M5 holes and one M6 hole were drilled and threaded. A ninth radial hole was also drilled and threaded into M6, to mount the sacrificial anode. The radial holes were distributed using a dividing head at Microfabriken.

### Pump module (främre lock, aluminiumskivor, bälg, blåsa, pump, ventil)

### Aluminum rack (plåt bockning, skruvar)


Mounted on the rear lid is an aluminum rack that holds the antenna, the thruster and the magnet for the dropweight. The rack is made by cutting out 3 mm thick aluminum sheet to 15 mm wide strips and then bending to the desired shape. The holes in the rack are drilled to fit M5 screws.
<br clear="right"/>
### Electronic mounting plates (vattenjet, bockning, blästring)

To mount electronics inside the glider, mounting plates were created in 2 mm thick aluminum sheet. They were cut out with a water jet at FUSE and then sandblasted to achieve a nice surface. Finally a sheet metal bending machine was used to bend the mounting plates.

The PCBs are not directly mounted on the aluminum plates but are instead placed on acrylic mounting plates. These have been cut out with a laser at CASE.

### Manouvre module (Vikter, stegmotorer, CAD)

### Battery module (Vikter, ballast)

The battery module was designed to accommodate space for one battery as well as space for ballast. On the sides, 12 steel rectangular blocks can be clamped, each weighing about 300 g. Furthermore, there are two steel plates with dimensions of 170x60x3 mm, weighing about 235 g each, which can be placed under the battery for additional ballast. 

### Antenna (Gjutning)

### Dropweight (Magnet gjutning + målad, vikter, zinc)

The dropweight system consists of an electropermanent magnet that holds a cylindrical weight. To waterproof the electrical contacts between SubConn and the magnet, heat shrink tubing was first used around the wires. Next, a molding socket was used to mold the cable to the SubConn connector with epoxy. The magnet, in turn, was also molded in epoxy to be waterproof. On the magnetic surface, a very thin layer of epoxy was used to try to obtain as strong magnetic strength as possible. The magnet was later spray-painted black and lacquered for both aesthetic reasons and to have a slightly more durable surface. 

The actual dropweights are steel cylinders with 50 mm diameter. To prevent corrosion, the weights were treated with zinc spray, which acts as a sacrificial anode.

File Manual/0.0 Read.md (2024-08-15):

# Intro - Manual
The following documents contain instructions for further development of the glider and instructions regarding the function of the glider.



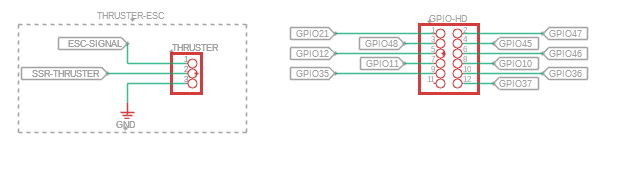
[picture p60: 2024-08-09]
Manual/Bilder/pin headers.png

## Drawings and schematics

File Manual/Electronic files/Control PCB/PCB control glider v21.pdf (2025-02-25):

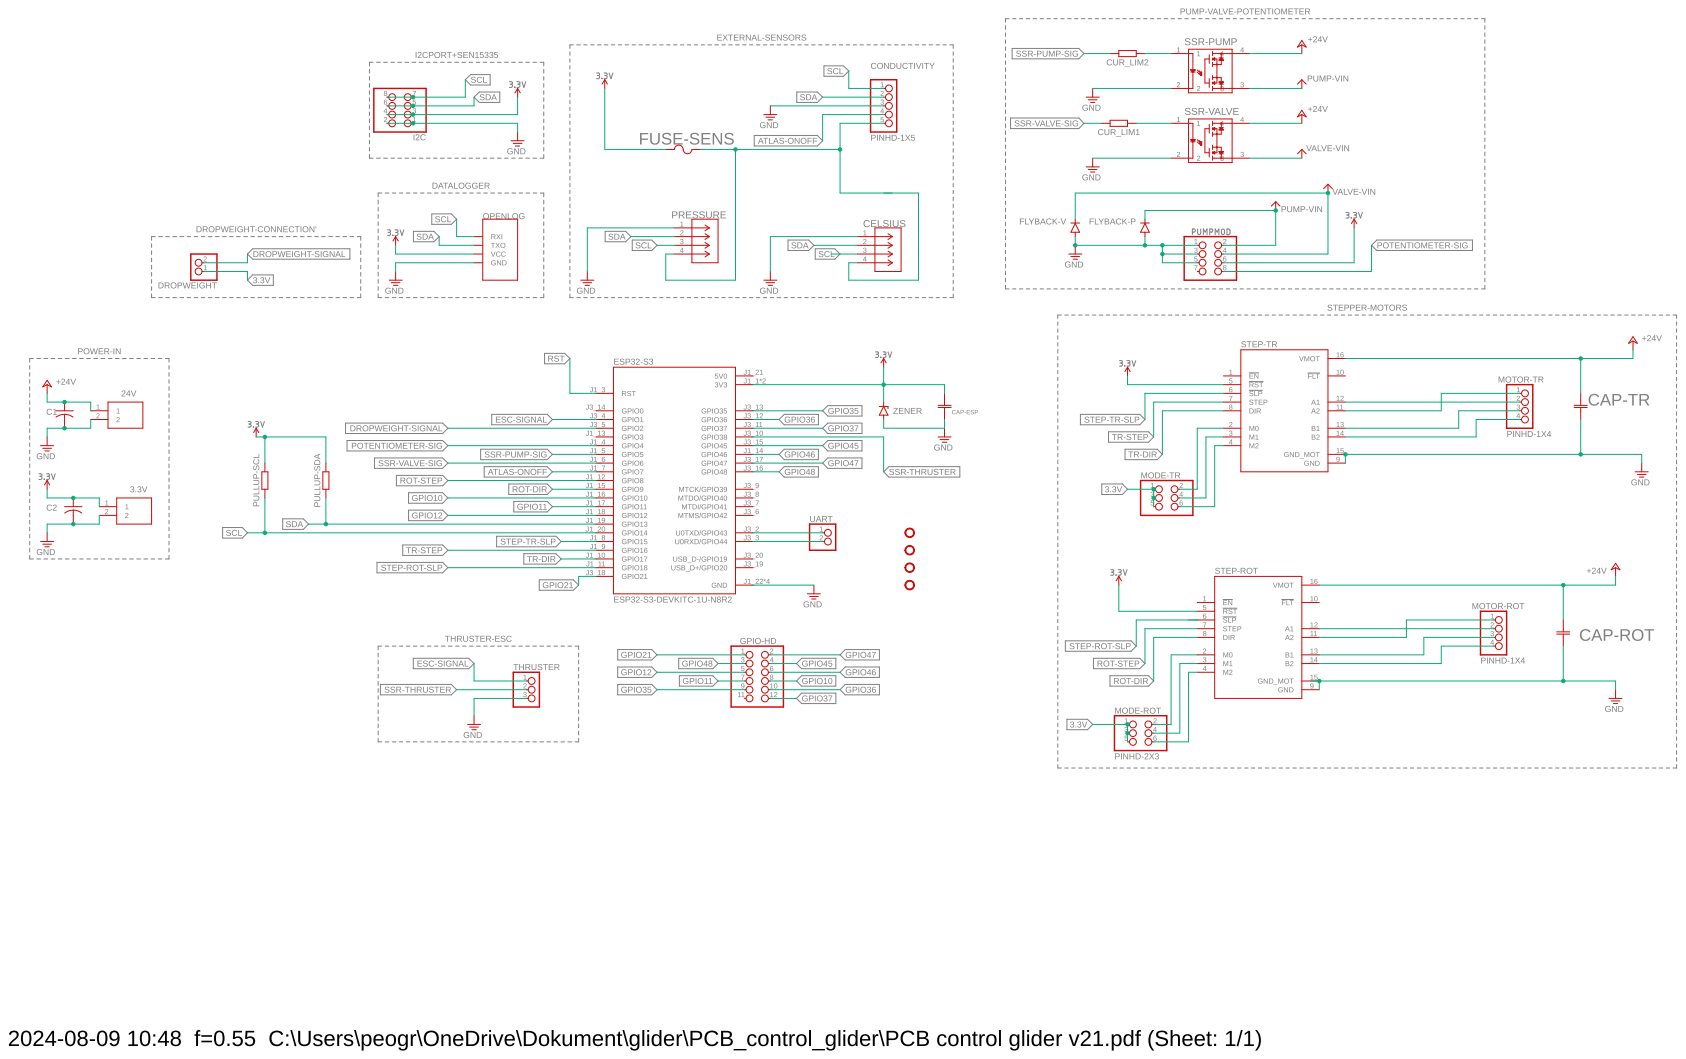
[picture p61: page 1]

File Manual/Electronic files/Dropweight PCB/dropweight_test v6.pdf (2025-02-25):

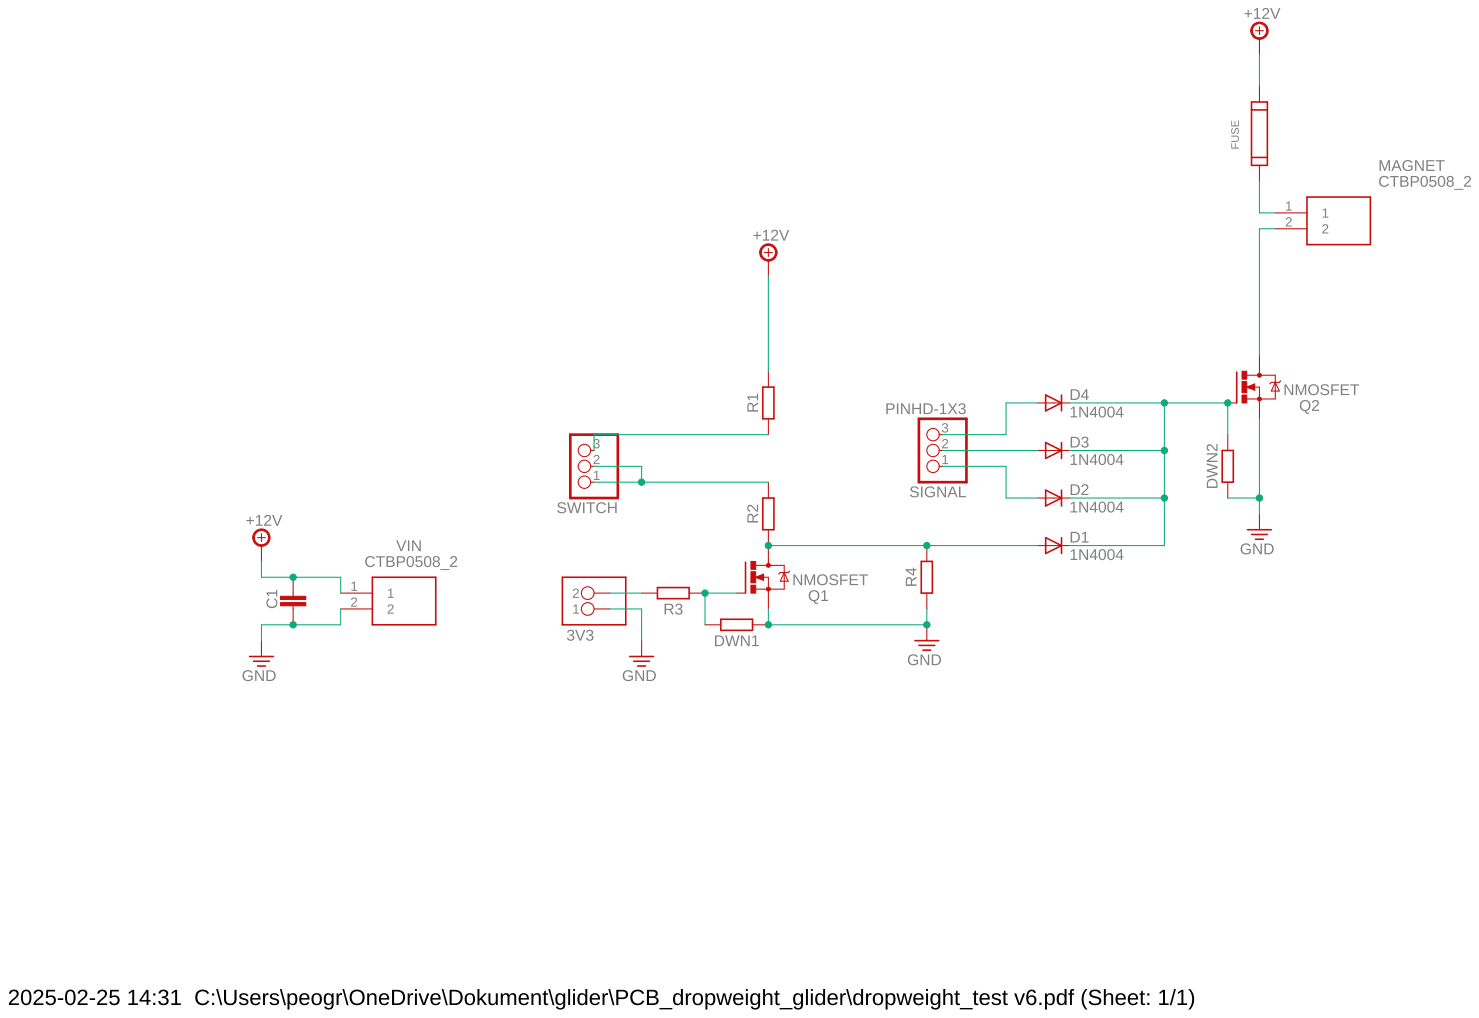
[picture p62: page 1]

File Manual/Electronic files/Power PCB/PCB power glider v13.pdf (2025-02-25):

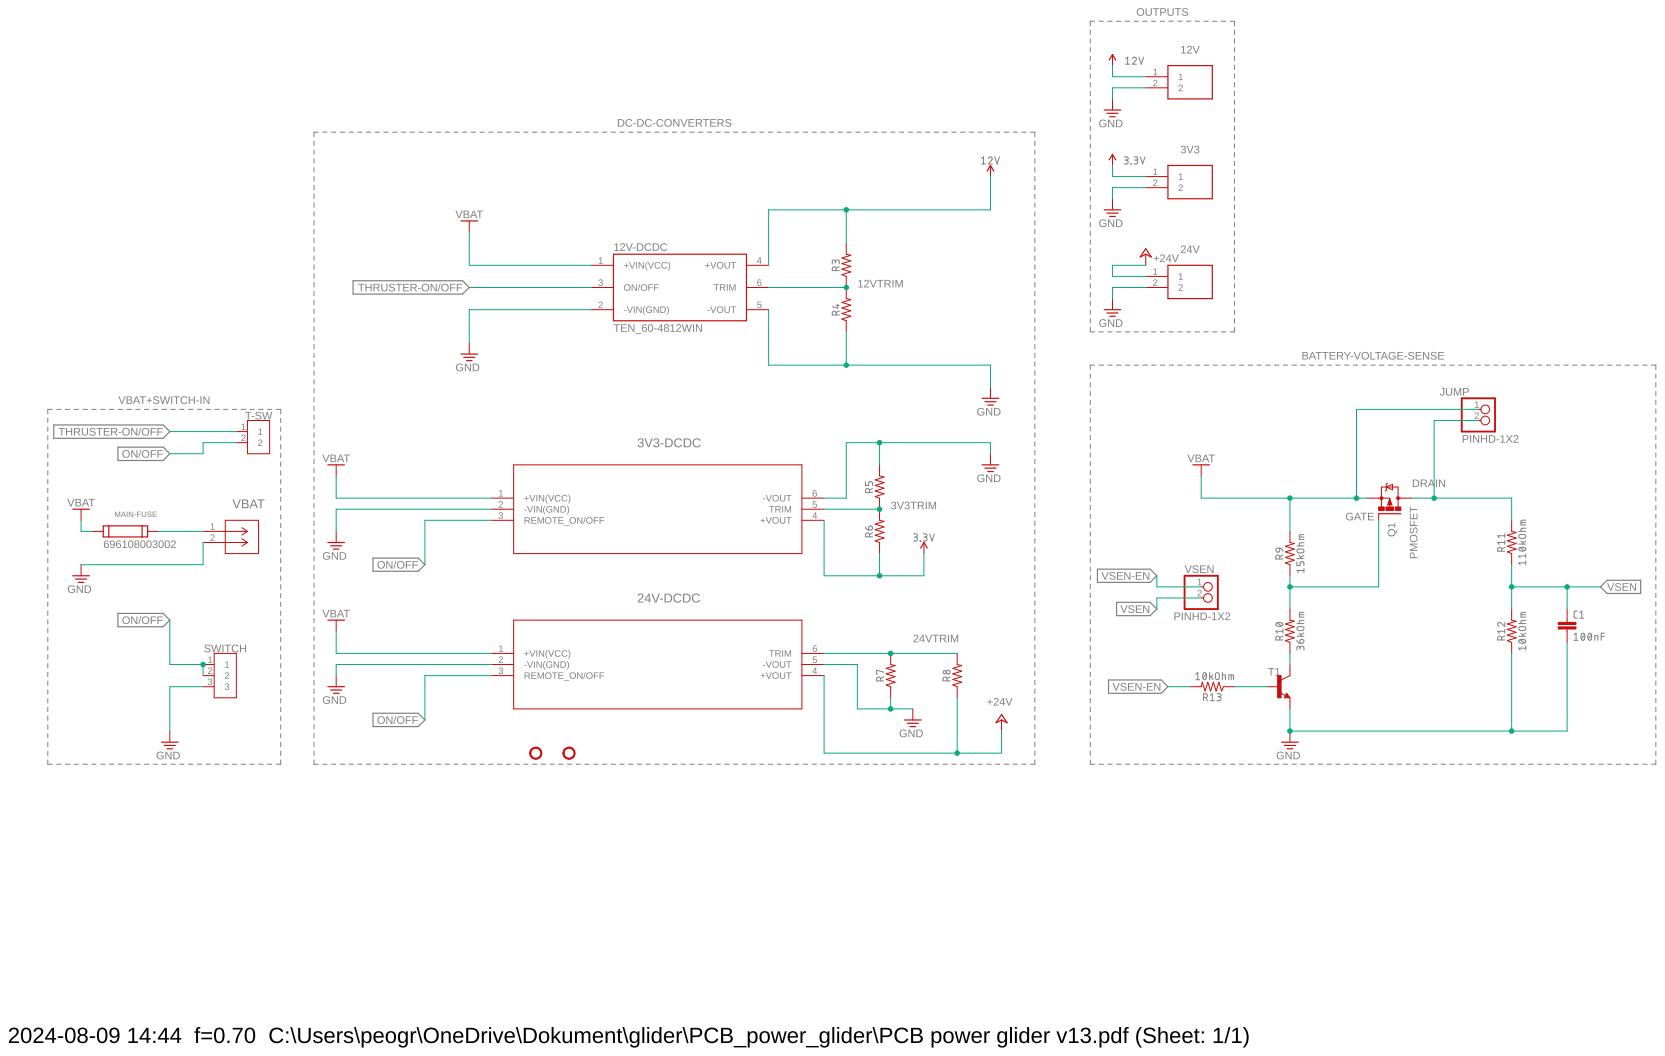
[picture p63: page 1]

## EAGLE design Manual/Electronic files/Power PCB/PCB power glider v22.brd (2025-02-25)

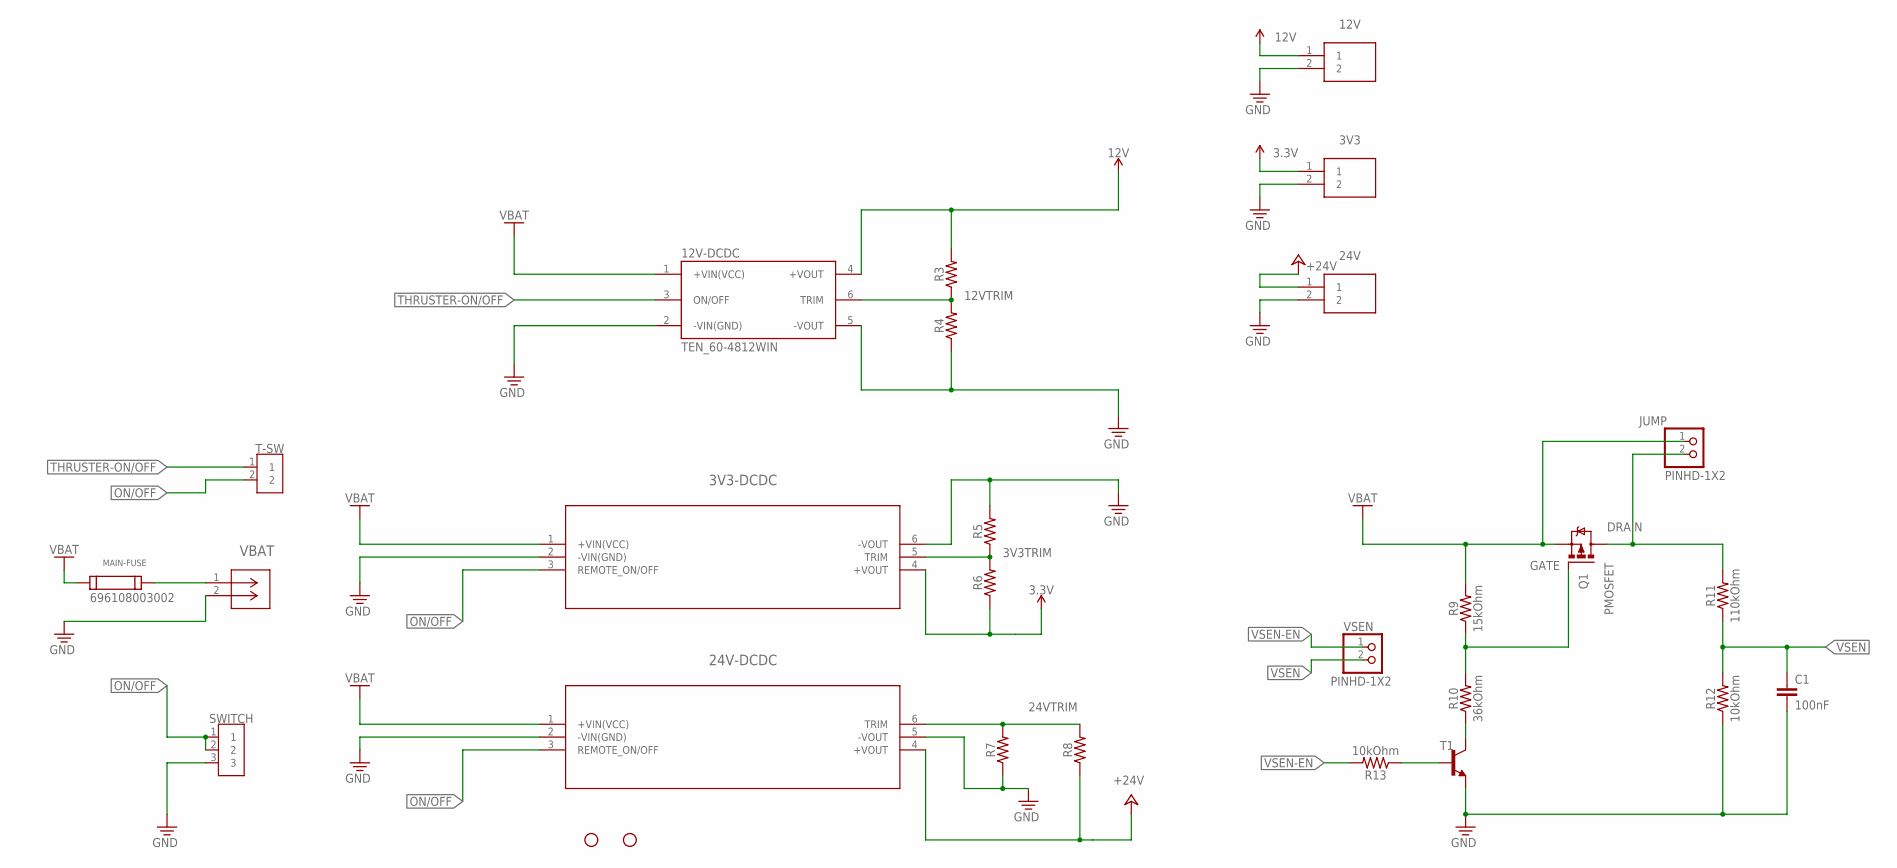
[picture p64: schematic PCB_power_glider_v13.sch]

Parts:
3V3, 12V, 24V: CTBP0508_2; CTBP05082
3V3-DCDC: THN_20-4810WIRTHN_20WIR_SINGLE_TRP; THN_20WIR_SINGLE_TRP
12V-DCDC: TEN_60-4812WIN; CONV_TEN_60-4812WIN
24V-DCDC: TEN_60-4815WINTEN_60WIN_TRP; TEN_60WIN_TRP
C1: 100nF; 0603
H1, H4: STAND-OFFTIGHT; STAND-OFF-TIGHT
JUMP: PINHD-1X2; 1X02
MAIN-FUSE: 696108003002
Q1: PMOSFET; SOT23
R3, R4, R5, R6, R7, R8: 0603
R9: 15kOhm; 0603
R10: 36kOhm; 0603
R11: 110kOhm; 0603
R12, R13: 10kOhm; 0603
SWITCH: 2828XX-3282834-3; TERMBLK_254-3N
T1: -NPN-SOT23-EBC; SOT23-EBC
T-SW: 2828XX-2282834-2; TERMBLK_254-2N
VBAT: NC6-P107-02CONN2_1437664-4_TEC; CONN2_1437664-4_TEC
VSEN: PINHD-1X2; 1X02

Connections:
3.3V: 3V3.1, 3V3-DCDC.4 (+VOUT), R6.1
3V3TRIM: 3V3-DCDC.5 (TRIM), R5.1, R6.2
12V: 12V.1, 12V-DCDC.4 (+VOUT), R3.2
12VTRIM: 12V-DCDC.6 (TRIM), R3.1, R4.2
24VTRIM: 24V-DCDC.6 (TRIM), R7.2, R8.2
+24V: 24V.1, 24V-DCDC.4 (+VOUT), R8.1
DRAIN: JUMP.2, Q1.3 (D), R11.2
GATE: Q1.1 (G), R9.1, R10.2
GND: 3V3.2, 3V3-DCDC.2 (-VIN(GND)), 3V3-DCDC.6 (-VOUT), 12V.2, 12V-DCDC.2 (-VIN(GND)), 12V-DCDC.5 (-VOUT), 24V.2, 24V-DCDC.2 (-VIN(GND)), 24V-DCDC.5 (-VOUT), C1.2, R4.1, R5.2, R7.1, R12.1, SWITCH.3, T1.E, VBAT.2
unnamed: MAIN-FUSE.2, VBAT.1
unnamed: R10.1, T1.C
unnamed: R13.1, T1.B
ON/OFF: 3V3-DCDC.3 (REMOTE_ON/OFF), 24V-DCDC.3 (REMOTE_ON/OFF), SWITCH.1, SWITCH.2, T-SW.2
THRUSTER-ON/OFF: 12V-DCDC.3 (ON/OFF), T-SW.1
VBAT: 3V3-DCDC.1 (+VIN(VCC)), 12V-DCDC.1 (+VIN(VCC)), 24V-DCDC.1 (+VIN(VCC)), JUMP.1, MAIN-FUSE.1, Q1.2 (S), R9.2
VSEN: C1.1, R11.1, R12.2, VSEN.2
VSEN-EN: R13.2, VSEN.1

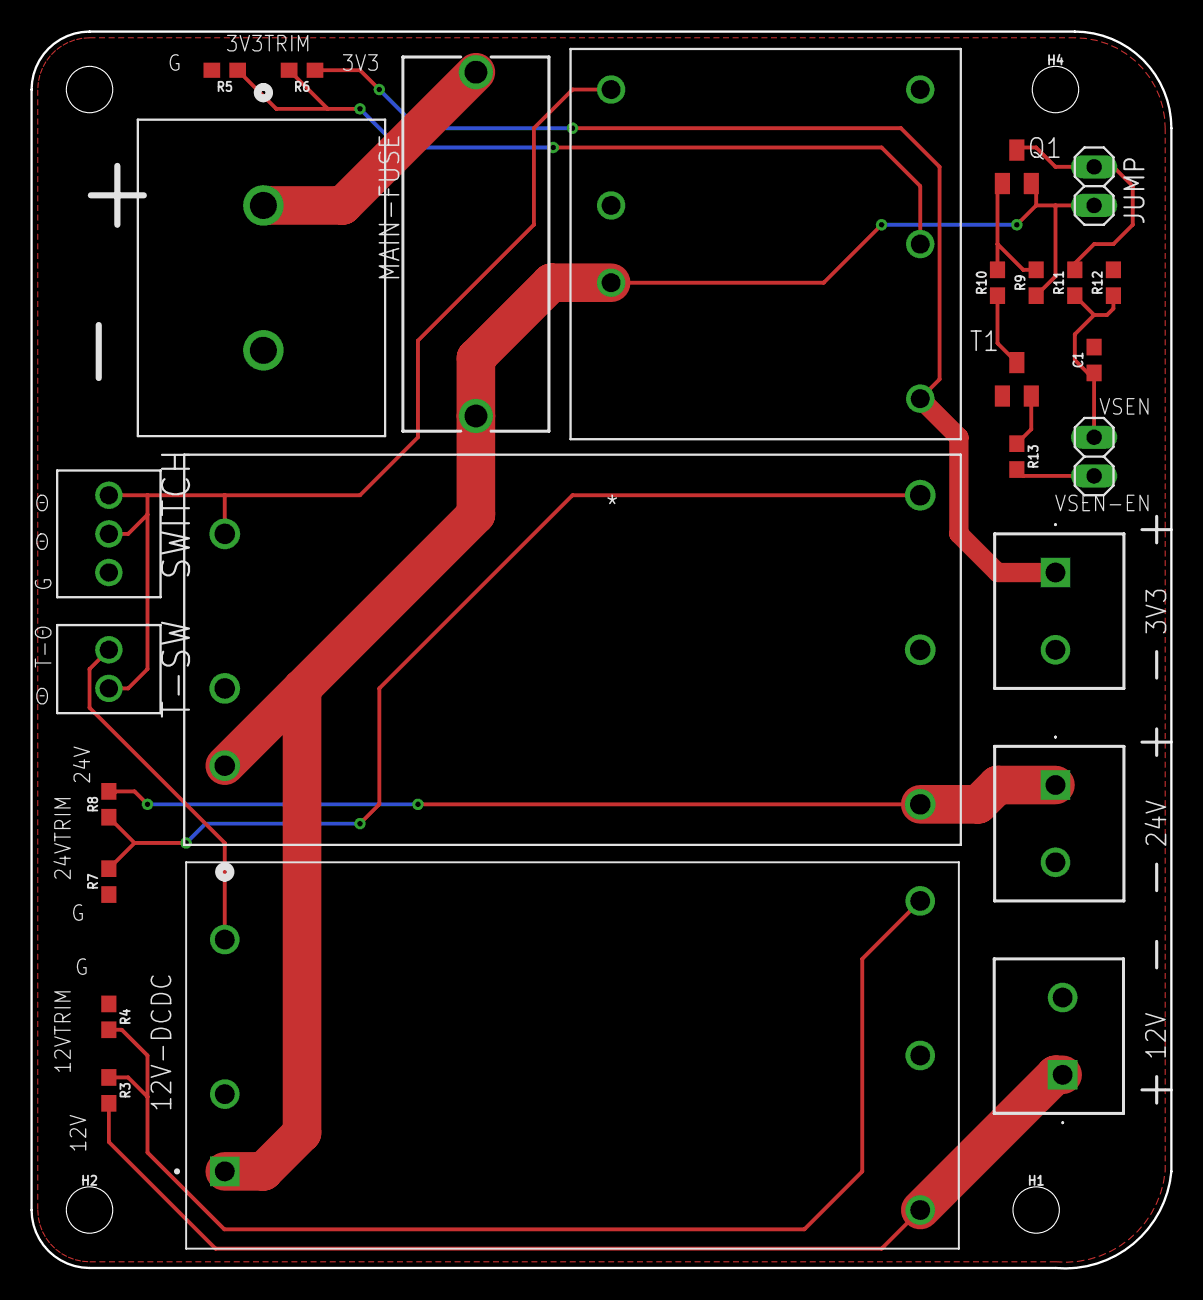
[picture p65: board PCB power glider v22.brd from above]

Board: 2 copper layers, 74.9 x 81.3 mm, 30 parts (0 on the bottom side), 17 nets.

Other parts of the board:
H2, H3: STAND-OFFTIGHT; STAND-OFF-TIGHT

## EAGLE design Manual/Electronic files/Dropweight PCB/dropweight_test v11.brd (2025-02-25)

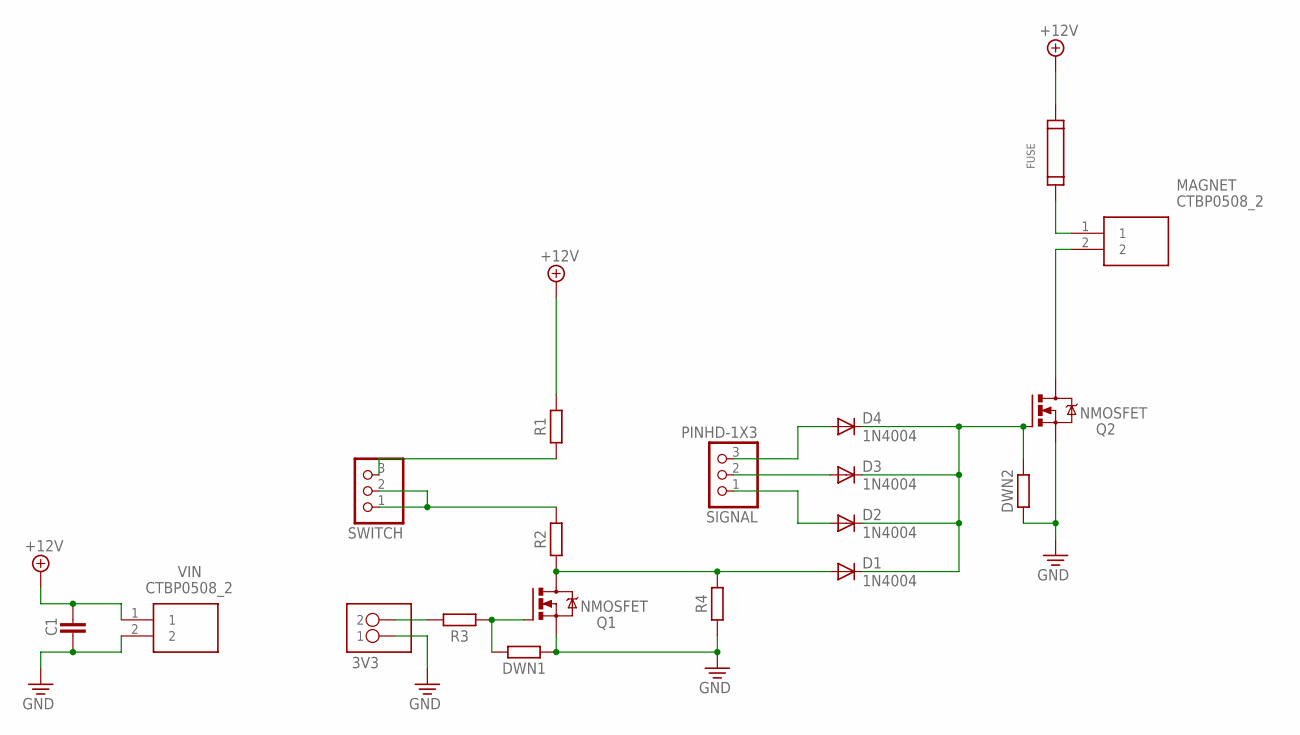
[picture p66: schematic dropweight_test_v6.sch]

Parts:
3V3: PINHD-1X02_1X02M; 1X02
C1: CAPACITORCERAMIC-2.54MM; CAP-THRU-2.54MM
D1, D2, D3, D4: 1N4004; DO41-10
DWN1, DWN2: RESISTOR-BACKUP_AXIAL-10.16MM-PITCH; RESAD1016W63L850D250B
FUSE: 696108003002
MAGNET: CTBP0508_2; CTBP05082
Q1, Q2: NMOSFET; TO220BV
R1, R2, R3, R4: RESISTOR-BACKUP_AXIAL-10.16MM-PITCH; RESAD1016W63L850D250B
SIGNAL: PINHD-1X3; 1X03
SWITCH: PINHD-1X3; 1X03
VIN: CTBP0508_2; CTBP05082

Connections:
3V3: 3V3.2, R3.2
+12V: C1.1, FUSE.2, R1.2, VIN.1
GND: 3V3.1, C1.2, DWN1.1, DWN2.1, Q1.S, Q2.S, R4.1, VIN.2
unnamed: R1.1, SWITCH.3
unnamed: R2.2, SWITCH.1, SWITCH.2
unnamed: D1.A, Q1.D, R2.1, R4.2
unnamed: DWN1.2, Q1.G, R3.1
unnamed: MAGNET.2, Q2.D
unnamed: D3.A, SIGNAL.2
unnamed: D4.A, SIGNAL.3
unnamed: D2.A, SIGNAL.1
unnamed: FUSE.1, MAGNET.1
unnamed: D1.C, D2.C, D3.C, D4.C, DWN2.2, Q2.G

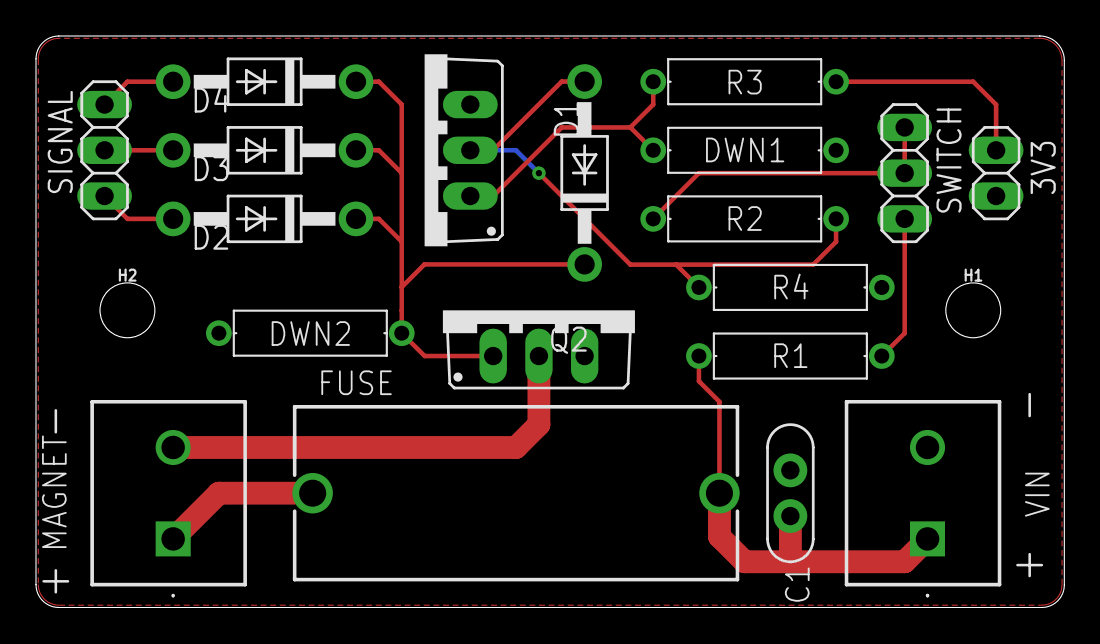
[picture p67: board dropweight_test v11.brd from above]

Board: 2 copper layers, 57.1 x 31.8 mm, 21 parts (0 on the bottom side), 13 nets.

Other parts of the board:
H1, H2: STAND-OFFTIGHT; STAND-OFF-TIGHT

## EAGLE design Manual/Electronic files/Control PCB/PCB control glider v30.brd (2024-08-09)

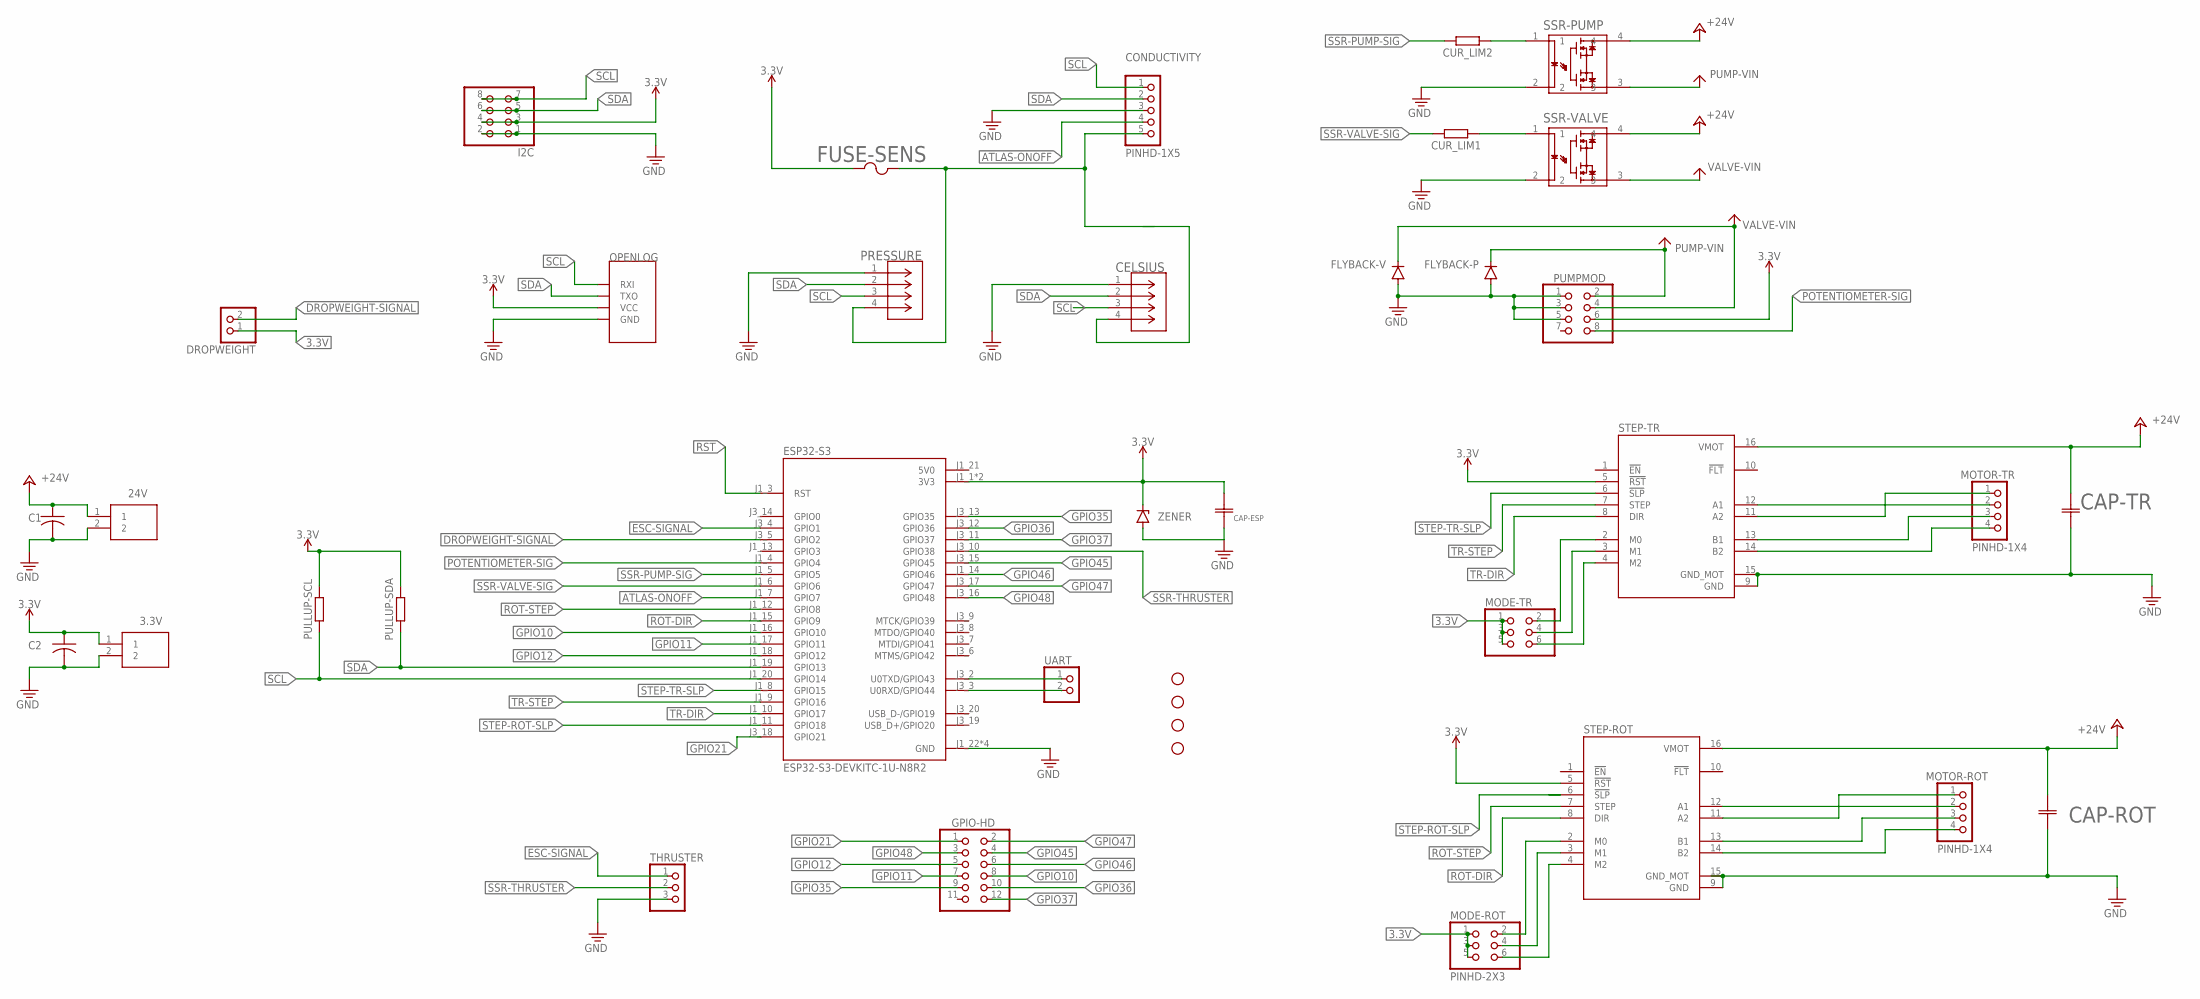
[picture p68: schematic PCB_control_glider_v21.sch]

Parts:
3.3V, 24V: CTBP0508_2; CTBP05082
C1, C2: ECA-1HM100; CAP_RADIAL_2MM
CAP-ESP: EEUHD1H101BCAP_PAN_8X11.5_PAN; CAP_PAN_8X11.5_PAN
CAP-ROT: EEUHD1H101BCAP_PAN_8X11.5_PAN; CAP_PAN_8X11.5_PAN
CAP-TR: EEUHD1H101BCAP_PAN_8X11.5_PAN; CAP_PAN_8X11.5_PAN
CELSIUS: BM04B-GHS-TBTCONN_BM04B-GHS-TBT_JST; CONN_BM04B-GHS-TBT_JST
CONDUCTIVITY: PINHD-1X5; 1X05
CUR_LIM1, CUR_LIM2: RESISTOR-BACKUP_AXIAL-10.16MM-PITCH; RESAD1016W63L850D250B
DROPWEIGHT: PINHD-1X2; 1X02
ESP32-S3: ESP32-S3-DEVKITC-1U-N8R2; XCVR_ESP32-S3-DEVKITC-1U-N8R2
FLYBACK-P: 1N4004; DO-41
FLYBACK-V: 1N4004; DO-41
FUSE-SENS: LVR033KFUS_LVR033_TYCO_TYC; FUS_LVR033_TYCO_TYC
GPIO-HD: PINHD-2X6; 2X06
H1, H2, H3, H4: STAND-OFFTIGHT; STAND-OFF-TIGHT
I2C: PINHD-2X4; 2X04
MODE-ROT: PINHD-2X3; 2X03
MODE-TR: PINHD-2X3; 2X03
MOTOR-ROT: PINHD-1X4; 1X04
MOTOR-TR: PINHD-1X4; 1X04
PRESSURE: BM04B-GHS-TBTCONN_BM04B-GHS-TBT_JST; CONN_BM04B-GHS-TBT_JST
PULLUP-SCL: RESISTOR-BACKUP_AXIAL-10.16MM-PITCH; RESAD1016W63L850D250B
PULLUP-SDA: RESISTOR-BACKUP_AXIAL-10.16MM-PITCH; RESAD1016W63L850D250B
PUMPMOD: PINHD-2X4; 2X04
QWIIC-OPENLOG: OPENLOG
SSR-PUMP: G3VM-61ARA-DIP4_THD_OMR; A-DIP4_THD_OMR
SSR-VALVE: G3VM-61ARA-DIP4_THD_OMR; A-DIP4_THD_OMR
STEP-ROT: DRV8825_STEPPER_MOTOR_DRIVER_CARRIER; IC_DRV8825_STEPPER_MOTOR_DRIVER_CARRIER
STEP-TR: DRV8825_STEPPER_MOTOR_DRIVER_CARRIER; IC_DRV8825_STEPPER_MOTOR_DRIVER_CARRIER
THRUSTER: PINHD-1X3; 1X03
UART: PINHD-1X2; 1X02
ZENER: ZENER_DIODE-AXIAL; DIODE-AXIAL

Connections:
3.3V: 3.3V.1, C2.1, CAP-ESP.1, DROPWEIGHT.1, ESP32-S3.J1_1 (3V3), ESP32-S3.J1_2 (3V3), FUSE-SENS.1, I2C.3, I2C.4, MODE-ROT.1, MODE-ROT.3, MODE-ROT.5, MODE-TR.1, MODE-TR.3, MODE-TR.5, PULLUP-SCL.2, PULLUP-SDA.2, PUMPMOD.6, QWIIC-OPENLOG.VCC, STEP-ROT.5 (!RST), STEP-TR.5 (!RST), ZENER.2 (C)
5V0: ESP32-S3.J1_21 (5V0)
+24V: 24V.1, C1.1, CAP-ROT.1, CAP-TR.1, SSR-PUMP.4, SSR-VALVE.4, STEP-ROT.16 (VMOT), STEP-TR.16 (VMOT)
ATLAS-ONOFF: CONDUCTIVITY.4, ESP32-S3.J1_7 (GPIO7)
DROPWEIGHT-SIGNAL: DROPWEIGHT.2, ESP32-S3.J3_5 (GPIO2)
ESC-SIGNAL: ESP32-S3.J3_4 (GPIO1), THRUSTER.1
GND: 3.3V.2, 24V.2, C1.2, C2.2, CAP-ESP.2, CAP-ROT.2, CAP-TR.2, CELSIUS.1, CONDUCTIVITY.3, ESP32-S3.J1_22 (GND), ESP32-S3.J3_1 (GND), ESP32-S3.J3_21 (GND), ESP32-S3.J3_22 (GND), FLYBACK-P.A, FLYBACK-V.A, I2C.1, I2C.2, PRESSURE.1, PUMPMOD.1, PUMPMOD.3, PUMPMOD.5, QWIIC-OPENLOG.GND, SSR-PUMP.2, SSR-VALVE.2, STEP-ROT.9 (GND), STEP-ROT.15 (GND_MOT), STEP-TR.9 (GND), STEP-TR.15 (GND_MOT), THRUSTER.3, ZENER.1 (A)
GPIO10: ESP32-S3.J1_16 (GPIO10), GPIO-HD.8
GPIO11: ESP32-S3.J1_17 (GPIO11), GPIO-HD.7
GPIO12: ESP32-S3.J1_18 (GPIO12), GPIO-HD.5
GPIO21: ESP32-S3.J3_18 (GPIO21), GPIO-HD.1
GPIO35: ESP32-S3.J3_13 (GPIO35), GPIO-HD.9
GPIO36: ESP32-S3.J3_12 (GPIO36), GPIO-HD.10
GPIO37: ESP32-S3.J3_11 (GPIO37), GPIO-HD.12
GPIO45: ESP32-S3.J3_15 (GPIO45), GPIO-HD.4
GPIO46: ESP32-S3.J1_14 (GPIO46), GPIO-HD.6
GPIO47: ESP32-S3.J3_17 (GPIO47), GPIO-HD.2
GPIO48: ESP32-S3.J3_16 (GPIO48), GPIO-HD.3
unnamed: ESP32-S3.J3_2 (U0TXD/GPIO43), UART.1
unnamed: ESP32-S3.J3_3 (U0RXD/GPIO44), UART.2
unnamed: MODE-TR.2, STEP-TR.2 (M0)
unnamed: MODE-TR.4, STEP-TR.3 (M1)
unnamed: MODE-TR.6, STEP-TR.4 (M2)
unnamed: CELSIUS.4, CONDUCTIVITY.5, FUSE-SENS.2, PRESSURE.4
unnamed: MODE-ROT.2, STEP-ROT.2 (M0)
unnamed: MODE-ROT.6, STEP-ROT.4 (M2)
unnamed: MODE-ROT.4, STEP-ROT.3 (M1)
unnamed: CUR_LIM2.1, SSR-PUMP.1
unnamed: CUR_LIM1.1, SSR-VALVE.1
POTENTIOMETER-SIG: ESP32-S3.J1_4 (GPIO4), PUMPMOD.8
PUMP-VIN: FLYBACK-P.C, PUMPMOD.2, SSR-PUMP.3
R-A1: MOTOR-ROT.2, STEP-ROT.12 (A1)
R-A2: MOTOR-ROT.1, STEP-ROT.11 (A2)
R-B1: MOTOR-ROT.3, STEP-ROT.13 (B1)
R-B2: MOTOR-ROT.4, STEP-ROT.14 (B2)
ROT-DIR: ESP32-S3.J1_15 (GPIO9), STEP-ROT.8 (DIR)
ROT-STEP: ESP32-S3.J1_12 (GPIO8), STEP-ROT.7 (STEP)
RST: ESP32-S3.J1_3 (RST)
SCL: CELSIUS.3, CONDUCTIVITY.1, ESP32-S3.J1_20 (GPIO14), I2C.7, I2C.8, PRESSURE.3, PULLUP-SCL.1, QWIIC-OPENLOG.RXI
SDA: CELSIUS.2, CONDUCTIVITY.2, ESP32-S3.J1_19 (GPIO13), I2C.5, I2C.6, PRESSURE.2, PULLUP-SDA.1, QWIIC-OPENLOG.TXO
SSR-PUMP-SIG: CUR_LIM2.2, ESP32-S3.J1_5 (GPIO5)
SSR-THRUSTER: ESP32-S3.J3_10 (GPIO38), THRUSTER.2
SSR-VALVE-SIG: CUR_LIM1.2, ESP32-S3.J1_6 (GPIO6)
STEP-ROT-SLP: ESP32-S3.J1_11 (GPIO18), STEP-ROT.6 (!SLP)
STEP-TR-SLP: ESP32-S3.J1_8 (GPIO15), STEP-TR.6 (!SLP)
T-A1: MOTOR-TR.2, STEP-TR.12 (A1)
T-A2: MOTOR-TR.1, STEP-TR.11 (A2)
T-B1: MOTOR-TR.3, STEP-TR.13 (B1)
T-B2: MOTOR-TR.4, STEP-TR.14 (B2)
TR-DIR: ESP32-S3.J1_10 (GPIO17), STEP-TR.8 (DIR)
TR-STEP: ESP32-S3.J1_9 (GPIO16), STEP-TR.7 (STEP)
VALVE-VIN: FLYBACK-V.C, PUMPMOD.4, SSR-VALVE.3

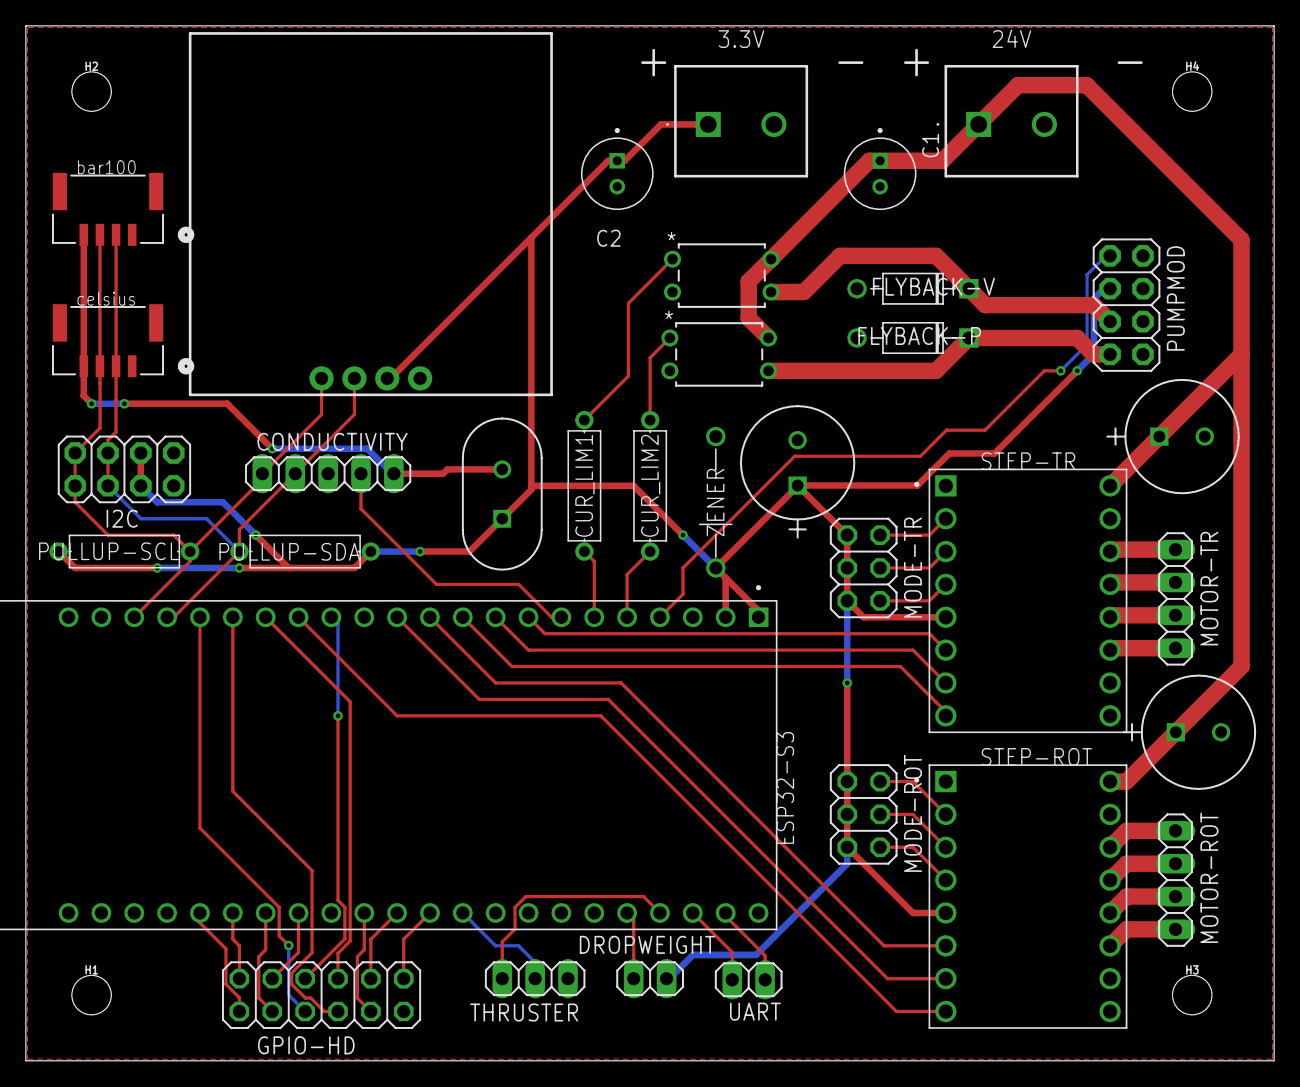
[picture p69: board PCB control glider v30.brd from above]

Board: 2 copper layers, 96.5 x 80.0 mm, 38 parts (0 on the bottom side), 50 nets.

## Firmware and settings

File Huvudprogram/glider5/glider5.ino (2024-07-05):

#include <Arduino.h>
#include <Wire.h>
#include <pgmspace.h>
#include <WiFi.h>
#include <WebServer.h>
#include <esp_wifi.h>
#include "page.h"               // Include the header file with HTML content


//.............................................................................

//Pin definitions for the ESP32 S3 

#define TRAN_DIR_PIN        17 //Translation motor direction pin
#define TRAN_STEP_PIN       16 //Translation motor step pin
#define TRAN_SLEEP_PIN      15 //Trasnlation motor sleep pin
#define ROT_DIR_PIN          9 //Rotation motor direction pin
#define ROT_STEP_PIN         8 //Rotation motor step pin
#define ROT_SLEEP_PIN       18 //Rotation motor sleep pin
#define SDA_PIN             13 //SDA pin for I2C communication
#define SCL_PIN             14 //SCL pin for I2C communication
#define MODE0               10 //Microstepping mode pin 0
#define MODE1               11 //Microstepping mode pin 1
#define MODE2               12 //Microstepping mode pin 2
#define SOFT_POT_PIN         2 //Pin connected to softpot wiper
#define PUMP_PIN             5 //Pin connected to pump
#define VALVE_PIN            6 //Pin connected to valve
#define DROPWEIGHT_PIN       4 //Pin connected to dropweight

//.............................................................................

//Stepper motor definitions

#include "DRV8825.h" //Library for the stepper motor driver

#define stepsPerRevolution 200 
#define STEPS_PER_CM 600    //Högst oklart, gör bättre mätning
#define STEPS_PER_DEGREE 10 //Ta reda på detta värde

#define TRANSLATION_MIN_POSITION_CM -1  //Maximum distance the translation motor can move the weight forwards
#define TRANSLATION_MAX_POSITION_CM 1   //Maximum distance the translation motor can move the weight backwards
#define TRANSLATIONMOTOR_STEP_SIZE 5    //Step size for the translation motor

#define ROTATION_MIN_DEGREE -90 //Minimum degree the rotation motor can move the weight
#define ROTATION_MAX_DEGREE 90 //Maximum degree the rotation motor can move the weight
#define ROTATIONMOTOR_STEP_SIZE 5 //Step size for the rotation motor

#define RPM 186 //The RPM of the motors

#define MICROSTEP 2 //Microstepping value

DRV8825 transtepper(stepsPerRevolution, TRAN_DIR_PIN, TRAN_STEP_PIN, TRAN_SLEEP_PIN, MODE0, MODE1, MODE2);  //Create an instance of the stepper motor driver for the translation motor
DRV8825 rotstepper(stepsPerRevolution, ROT_DIR_PIN, ROT_STEP_PIN, ROT_SLEEP_PIN, MODE0, MODE1, MODE2); //Create an instance of the stepper motor driver for the rotation motor

//.............................................................................

//Keep track of the number of dives the glider has done
int n_dyk = 0;
long totalNumberofDives = 0; // Total number of dives the glider has done since the start of the program

//Flag to check if the dropweight has been released
bool dropweight = false;

bool isIdle = false;
bool isDiving = false;
bool isCalibrating = false;

//Flags that are used to control the movement of the glider when in Idle state. 
//Can be set to true via the SeaGUL webpage.
bool rotatingLeft = false;
bool rotatingRight = false;
bool movingForward = false;
bool movingBackward = false;


//Values that are displayed on the SeaGUL webpage
float displaypitch = 0;
float displayroll = 0;
float displayyaw = 0;
float displaypressure = 0;
float displaytemperature = 0;
float displaypotentiometer = 0;

//Used to keep track on where the weight is positioned
float nextPosition = 0;
float nextDegree = 0;

unsigned long stateStartMillis = 0; // Variable to store the start time of the states GlidingDown and GlidingUp

// Struct to hold sensor data
struct SensorData {
    float pitch;
    float roll;
    float yaw;
    float depth;
    float pressure;
    float potentiometer;
    float temperature;
};
QueueHandle_t sensorDataQueue; // Queue to hold sensor data

// Enum to keep track of the state of the glider
enum StepperState {
    Idle,
    Diving,
    Calibrating,
    GlidingDown,
    GlidingUp,
    DropWeight,
    Surface
};
StepperState gliderState = Idle; // Initial state of the glider

// Pressure sensor
#include <KellerLD.h>
KellerLD Psensor;

// Temperature sensor
#include <TSYS01.h>
TSYS01 Tsensor;

// Orientation sensor
#include <ICM_20948.h>
#define AD0_VAL 1 //The value of the AD0 pin on the ICM-20948 sensor
ICM_20948_I2C myICM;

// SD-card logging
#include "SparkFun_Qwiic_OpenLog_Arduino_Library.h"
OpenLog myLog;
String fileName = "SD-test10_240612.txt"; //Name of the file that the data will be stored in

//.............................................................................

// Function prototypes

void openLogSetup();
void moveRotationMotor(SensorData receivedData, float &currentDegree, float &rollSP, bool &rotationmotorRunning);
void moveTranslationMotor(SensorData receivedData, float &currentPosition, float &pitchSP, bool translationmotorRunning);
void glidercontrol(void* pvParameters);
void datagathering(void* pvParameters);
void writeSD(String measurement) {
  myLog.append(fileName); //Bestämmer att vi ska sriva i denna filen 
  myLog.println(measurement); //Skriver till filen
  myLog.syncFile();
}

//.............................................................................

//NETWORKING

// Network credentials
const char* ssid = "SEAGUL";
const char* password = "0123456789";

// Custom IP configuration
IPAddress local_IP(192, 168, 4, 1);  // Change this to your desired IP
IPAddress gateway(192, 168, 4, 1);
IPAddress subnet(255, 255, 255, 0);

// Create a WebServer object on port 80
WebServer server(80);

// Global variable to be controlled by the buttons
String currentState = "Idle";

// Handle root path
void handleRoot() {
  String pageWithSignalStrength = String(page_html);
  server.send(200, "text/html", pageWithSignalStrength);
}

// Handle update
void handleUpdate() {
  if (server.hasArg("state")) {
    currentState = server.arg("state");
    Serial.print("Current state updated to: ");
    Serial.println(currentState);
    server.send(200, "text/plain", "OK");
  } else {
    server.send(400, "text/plain", "Bad Request");
  }
}

// Handle when idle button is pressed
void handleIdle() {
  // isIdle = true;
  // isDiving = false;
  // isCalibrating = false;
  gliderState = Idle;
  Serial.println("Set to Idle");
  server.send(200, "text/plain", "Set to Idle");
}

// Handle when intitiate dive button is pressed
void handleInitiateDive() {
  // isIdle = false;
  // isDiving = true;
  // isCalibrating = false;
  gliderState = Diving;
  Serial.println("Dive Initiated");
  server.send(200, "text/plain", "Dive Initiated");
}

// Handle when calibrate button is pressed
void handleCalibrate() {
  // isIdle = false;
  // isDiving = false;
  // isCalibrating = true;
  gliderState = Calibrating;
  Serial.println("Calibration Started");
  server.send(200, "text/plain", "Calibration Started");
}

// Handle when rotate left button is pressed
void handleRotateLeft() {
  rotatingLeft = true;
//   Serial.println("Rotate Left command received");
//   Serial.print("rotatingLeft: ");
//   Serial.println(rotatingLeft);
  server.send(200, "text/plain", "Rotate Left started");
}

// Handle when rotate right button is pressed
void handleRotateRight() {
  rotatingRight = true;
//   Serial.println("Rotate Right command received");
//   Serial.print("rotatingRight: ");
//   Serial.println(rotatingRight);
  server.send(200, "text/plain", "Rotate Right started");
}

// Handle when move forward button is pressed
void handleMoveForward() {
  movingForward = true;
//   Serial.println("Move Forward command received");
//   Serial.print("movingForward: ");
//   Serial.println(movingForward);
  server.send(200, "text/plain", "Move Forward started");
}

// Handle when move backward button is pressed
void handleMoveBackward() {
  movingBackward = true;
//   Serial.println("Move Backward command received");
//   Serial.print("movingBackward: ");
//   Serial.println(movingBackward);
  server.send(200, "text/plain", "Move Backward started");
}

// Handle when rotate left button is released
void handleStopRotateLeft() {
  rotatingLeft = false;
//   Serial.println("Rotate Left stopped");
//   Serial.print("rotatingLeft: ");
//   Serial.println(rotatingLeft);
  server.send(200, "text/plain", "Rotate Left stopped");
}

// Handle when rotate right button is released
void handleStopRotateRight() {
  rotatingRight = false;
  server.send(200, "text/plain", "Rotate Right stopped");
}

// Handle when move forward button is released
void handleStopMoveForward() {
  movingForward = false;
  server.send(200, "text/plain", "Move Forward stopped");
}

// Handle when move backward button is released
void handleStopMoveBackward() {
  movingBackward = false;
  server.send(200, "text/plain", "Move Backward stopped");
}

// Function to generate random number 
float randomFloat(float minValue, float maxValue) {
  return minValue + (float)rand() / ((float)RAND_MAX / (maxValue - minValue));
}

// Handle signal strength
String getConnectedDevices() {
  String deviceInfo = "[";
  wifi_sta_list_t wifi_sta_list;
  esp_wifi_ap_get_sta_list(&wifi_sta_list);

  for (int i = 0; i < wifi_sta_list.num; i++) {
    if (i > 0) deviceInfo += ",";
    wifi_sta_info_t station = wifi_sta_list.sta[i];
    char macStr[18];
    snprintf(macStr, sizeof(macStr), "%02X:%02X:%02X:%02X:%02X:%02X",
             station.mac[0], station.mac[1], station.mac[2],
             station.mac[3], station.mac[4], station.mac[5]);
    deviceInfo += "{";
    deviceInfo += "\"mac\":\"" + String(macStr) + "\",";
    deviceInfo += "\"rssi\":" + String(station.rssi);
    deviceInfo += "}";
  }

  deviceInfo += "]";
  return deviceInfo;
}

// Handle data
void handleData() {
  String json = "{";
  json += "\"currentState\":\"" + currentState + "\",";
  json += "\"devices\":" + getConnectedDevices() + ",";
  json += "\"waterTemperature\":" + String(displaytemperature) + ",";
  json += "\"pressure\":" + String(displaypressure) + ",";
  json += "\"salinity\":" + String(randomFloat(30.0, 50.0)) + ",";
  json += "\"pitch\":" + String(displaypitch) + ",";
  json += "\"roll\":" + String(displayroll) + ",";
  json += "\"yaw\":" + String(displayyaw) + ",";
  json += "\"batteryVoltage\":" + String(randomFloat(22.0, 38.5)) + ",";
  json += "\"compassCourse\":" + String(randomFloat(0.0, 360.0)) + ",";
  json += "\"gnssCoordinates\":\"" + String(randomFloat(-90.0, 90.0), 6) + ", " + String(randomFloat(-180.0, 180.0), 6) + "\",";
  json += "\"internalTemperature\":" + String(randomFloat(15.0, 25.0)) + ",";
  json += "\"internalPressure\":" + String(randomFloat(0.0, 1.0)) + ",";
  json += "\"internalHumidity\":" + String(randomFloat(10.0, 30.0)) + ",";
  json += "\"adcValue\":" + String(displaypotentiometer);
  json += "}";
  server.send(200, "application/json", json);
}

void setup() {
    Serial.begin(115200);

    transtepper.begin(RPM);
    transtepper.enable();
    rotstepper.begin(RPM);
    rotstepper.enable();

    pinMode(TRAN_SLEEP_PIN, OUTPUT);
    pinMode(TRAN_DIR_PIN, OUTPUT);
    pinMode(ROT_SLEEP_PIN, OUTPUT);
    pinMode(ROT_DIR_PIN, OUTPUT);

    pinMode(SOFT_POT_PIN, INPUT);

    pinMode(PUMP_PIN, OUTPUT);
    pinMode(VALVE_PIN, OUTPUT);

    pinMode(DROPWEIGHT_PIN, OUTPUT);

    Wire.begin(SDA_PIN, SCL_PIN);
    Wire.setClock(400000);

    bool initialized = false;
    while (!initialized) {
        myICM.begin(Wire, AD0_VAL);
        Serial.print(F("Initialization of the sensor returned: "));
        Serial.println(myICM.statusString());
        if (myICM.status != ICM_20948_Stat_Ok) {
            Serial.println("Trying again...");
            delay(500);
        } else {
            initialized = true;
        }
    }
    Serial.println("Device connected!");

    bool success = true;
    success &= (myICM.initializeDMP() == ICM_20948_Stat_Ok);
    success &= (myICM.enableDMPSensor(INV_ICM20948_SENSOR_GAME_ROTATION_VECTOR) == ICM_20948_Stat_Ok);
    // success &= (myICM.setDMPODRrate(DMP_ODR_Reg_Quat6, 0) == ICM_20948_Stat_Ok);
        // Enable the FIFO
    success &= (myICM.enableFIFO() == ICM_20948_Stat_Ok);

    // Enable the DMP
    success &= (myICM.enableDMP() == ICM_20948_Stat_Ok);

    // Reset DMP
    success &= (myICM.resetDMP() == ICM_20948_Stat_Ok);

    // Reset FIFO
    success &= (myICM.resetFIFO() == ICM_20948_Stat_Ok);

    if (success) {
        Serial.println("DMP configuration successful");
    } else {
        Serial.println("DMP configuration failed");
    }

    Psensor.init();
    Psensor.setFluidDensity(997); // kg/m^3 (freshwater, 1029 for seawater)
    if (Psensor.isInitialized()) {
        Serial.println("Pressure sensor connected.");
    } else {
        Serial.println("Pressure sensor not connected.");
    }

    Tsensor.init();
    while (!Tsensor.init()) {
        Serial.println("TSYS01 device failed to initialize!");
        delay(1000);
    }

    openLogSetup();

    sensorDataQueue = xQueueCreate(10, sizeof(SensorData));
    if (sensorDataQueue == NULL) {
        Serial.println("Failed to create queue");
        return;
    }

    xTaskCreatePinnedToCore(
        datagathering,                       // Function to implement the task
        "Measurement and storing of data",   // Name of the task
        2048,                                // Stack size in bytes
        NULL,                                // Task input parameter
        1,                                   // Priority of the task
        NULL,                                // Task handle.
        0                                    // Core where the task should run
    );

    xTaskCreatePinnedToCore(
        glidercontrol,                      // Function to implement the task
        "descision making for glider",      // Name of the task
        2048,                               // Stack size in bytes
        NULL,                               // Task input parameter
        1,                                  // Priority of the task
        NULL,                               // Task handle.
        1                                   // Core where the task should run
    );

    WiFi.softAP(ssid, password);
    WiFi.softAPConfig(local_IP, gateway, subnet);

    server.on("/", handleRoot);
    server.on("/update", handleUpdate);
    server.on("/data", handleData);
    server.on("/idle", handleIdle);
    server.on("/initiateDive", handleInitiateDive);
    server.on("/calibrate", handleCalibrate);
    server.on("/rotateLeft", handleRotateLeft);
    server.on("/rotateRight", handleRotateRight);
    server.on("/moveForward", handleMoveForward);
    server.on("/moveBackward", handleMoveBackward);
    server.on("/stopRotateLeft", handleStopRotateLeft);
    server.on("/stopRotateRight", handleStopRotateRight);
    server.on("/stopMoveForward", handleStopMoveForward);
    server.on("/stopMoveBackward", handleStopMoveBackward);
    
    server.begin();
    Serial.println("HTTP server started");


}

void loop() {
    server.handleClient();
}

void openLogSetup() {
  myLog.begin();

//   Serial.begin(115200); //9600bps is used for debug statements
  Serial.println("OpenLog Status Test");

  byte status = myLog.getStatus();

  Serial.print("Status byte: 0x");
  if(status < 0x10) {
    Serial.print("0");
  }
  Serial.println(status, HEX);

  if (status == 0xFF) {
    Serial.println("OpenLog failed to respond. Freezing.");
    while(1); //Freeze!
  }

  if(status & 1<<STATUS_SD_INIT_GOOD) {
    Serial.println("SD card is good");
  }  
  else {
    Serial.println("SD init failure. Is the SD card present? Formatted?");
  }
  if(status & 1<<STATUS_IN_ROOT_DIRECTORY) {    
    Serial.println("Root directory open");
  }
  else {
    Serial.println("Root failed to open. Is SD card present? Formatted?");
  }
  if (status & 1<<STATUS_FILE_OPEN) {
    Serial.println("Log file open and ready for recording");
  }
  else {
    Serial.println("No log file open. Use append command to start a new log.");
  }
  Serial.println("Done!");
  myLog.create(fileName);
  myLog.syncFile();
}

void moveRotationMotor (SensorData receivedData, float &currentDegree, float &rollSP, bool &rotationmotorRunning) {
    float roll_error = rollSP - (receivedData.roll * 180 / PI);
    int rot_direction = (roll_error < 0) ? 1 : -1;
    nextDegree = currentDegree + rot_direction * (ROTATIONMOTOR_STEP_SIZE / (float)STEPS_PER_DEGREE);

    if (fabs(roll_error) > 5) {
        if (!rotationmotorRunning) {
            digitalWrite(ROT_SLEEP_PIN, HIGH);
            rotationmotorRunning = true;
        }

        if (nextDegree < ROTATION_MAX_DEGREE && nextDegree > ROTATION_MIN_DEGREE) {
            rotstepper.setMicrostep(1);
            rotstepper.move(rot_direction > 0 ? ROTATIONMOTOR_STEP_SIZE : -ROTATIONMOTOR_STEP_SIZE);
            currentDegree = nextDegree;
        } else {
            if (!rotationmotorRunning) {
                digitalWrite(ROT_SLEEP_PIN, HIGH);
                rotationmotorRunning = true;
            }

            if ((rot_direction > 0 && currentDegree >= ROTATION_MAX_DEGREE) || (rot_direction < 0 && currentDegree <= ROTATION_MIN_DEGREE)) {
                rotstepper.setMicrostep(1);
                rotstepper.move(rot_direction > 0 ? ROTATIONMOTOR_STEP_SIZE : -ROTATIONMOTOR_STEP_SIZE);
                currentDegree = nextDegree;
            }
        }
    } else {
        if (rotationmotorRunning) {
            digitalWrite(ROT_SLEEP_PIN, LOW);
            rotationmotorRunning = false;
        }
    }
}

void moveTranslationMotor (SensorData receivedData, float &currentPosition, float &pitchSP, bool translationmotorRunning) {
    //Translation motor
    float pitch_error = pitchSP - (receivedData.pitch * 180 / PI);
    int transl_direction = (pitch_error < 0) ? 1 : -1;
    nextPosition = currentPosition + transl_direction * (TRANSLATIONMOTOR_STEP_SIZE / (float)STEPS_PER_CM);

   if (fabs(pitch_error) > 5) {
        if (!translationmotorRunning) {
            digitalWrite(TRAN_SLEEP_PIN, HIGH);
            translationmotorRunning = true;
        }

        if (nextPosition < TRANSLATION_MAX_POSITION_CM && nextPosition > TRANSLATION_MIN_POSITION_CM) {
            transtepper.setMicrostep(1);
            transtepper.move(transl_direction > 0 ? TRANSLATIONMOTOR_STEP_SIZE : -TRANSLATIONMOTOR_STEP_SIZE);
            currentPosition = nextPosition;
        } else {
            if (!translationmotorRunning) {
                digitalWrite(TRAN_SLEEP_PIN, HIGH);
                translationmotorRunning = true;
            }

            if ((transl_direction > 0 && currentPosition >= TRANSLATION_MAX_POSITION_CM) || (transl_direction < 0 && currentPosition <= TRANSLATION_MIN_POSITION_CM)) {
                transtepper.setMicrostep(1);
                transtepper.move(transl_direction > 0 ? TRANSLATIONMOTOR_STEP_SIZE : -TRANSLATIONMOTOR_STEP_SIZE);
                currentPosition = nextPosition;
            }
        }
    } else {
        if (translationmotorRunning) {
            digitalWrite(TRAN_SLEEP_PIN, LOW);
            translationmotorRunning = false;
        }
    }
}

void controlRotationMotor (float &rotation_direction, float &currentDegree, bool rotationmotorRunning) {
    nextDegree = currentDegree + rotation_direction * (ROTATIONMOTOR_STEP_SIZE / (float)STEPS_PER_DEGREE);

    if (rotation_direction > 0) {
        if (nextDegree < ROTATION_MAX_DEGREE && nextDegree > ROTATION_MAX_DEGREE) {
            rotstepper.setMicrostep(MICROSTEP);
            rotstepper.move(ROTATIONMOTOR_STEP_SIZE);
            currentDegree = nextDegree;
            Serial.println(currentDegree);
            
        } else {
            if (!rotationmotorRunning) {
                digitalWrite(ROT_SLEEP_PIN, HIGH);
                rotationmotorRunning = true;
            }

            if ((rotation_direction > 0 && currentDegree >= ROTATION_MIN_DEGREE)) {
                rotstepper.setMicrostep(MICROSTEP);
                rotstepper.move(ROTATIONMOTOR_STEP_SIZE);
                currentDegree = nextDegree;
                Serial.println(currentDegree);
            }

        }    
    }

    if (rotation_direction < 0) {

        if (nextDegree < ROTATION_MAX_DEGREE && nextDegree > ROTATION_MAX_DEGREE) {
            rotstepper.setMicrostep(MICROSTEP);
            rotstepper.move(-ROTATIONMOTOR_STEP_SIZE);
            currentDegree = nextDegree;
            Serial.println(currentDegree);

        } else {

            if (!rotationmotorRunning) {
                digitalWrite(ROT_SLEEP_PIN, HIGH);
                rotationmotorRunning = true;
            }

            if ((rotation_direction < 0 && currentDegree <= ROTATION_MIN_DEGREE)) {
                rotstepper.setMicrostep(MICROSTEP);
                rotstepper.move(-ROTATIONMOTOR_STEP_SIZE);
                currentDegree = nextDegree;
                Serial.println(currentDegree);
            }   

        }
    }
}
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

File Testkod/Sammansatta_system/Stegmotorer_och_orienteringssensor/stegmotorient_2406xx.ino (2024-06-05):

#include <Wire.h>
#include "ICM_20948.h"
#include <freertos/FreeRTOS.h>
#include <freertos/task.h>
#include <freertos/queue.h>
#include <freertos/semphr.h>


#define SDA_PIN 17
#define SCL_PIN 16

#define AD0_VAL 1


// Define stepper motor connections and steps per revolution:
#define dirPin 5
#define stepPin 6
#define sleepPin 7
#define stepsPerRevolution 200

// ICM_20948_AGMT_t agmt;

ICM_20948_I2C myICM;

const float real_pitch = -20 * PI / 180;
// const float real_roll = 0;
// const float real_yaw = ...;

QueueHandle_t sensorDataQueue;


void Orientation(void *pvParameters) {
    while(true) {
        if (myICM.dataReady()) {
            
            myICM.getAGMT();


        }

    }

}



void Vehiclecontrol(void *pvParameters) {


}


void setup() {
    pinMode(stepPin, OUTPUT);
    pinMode(dirPin, OUTPUT);
    pinMode(sleepPin, OUTPUT);
    pinMode(LED_BUILTIN, OUTPUT);
    Wire.begin(SDA_PIN, SCL_PIN);
    Wire.setClock(400000);
    Serial.begin(115200);

    xTaskCreatePinnedToCore(Orientation, "Orienteringsdata", 10000, NULL, 1, NULL, 1);

    xTaskCreatePinnedToCore(Vehiclecontrol, "Reglering av tyngdpaket", 10000, NULL, 1, NULL, 1);

    bool initialized = false;
    while (!initialized) { 
        myICM.begin(Wire, AD0_VAL);
        Serial.print(F("Initialization of the sensor returned: "));
        Serial.println(myICM.statusString());
        if (myICM.status != ICM_20948_Stat_Ok) {
        Serial.println("Trying again...");
        delay(500);
        }
        else {
        initialized = true;
        }
    }  
}

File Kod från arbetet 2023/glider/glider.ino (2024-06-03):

#include <Wire.h>
#include <Adafruit_Sensor.h>
#include <Adafruit_BNO055.h>
#include <utility/imumaths.h>
#include <Stepper.h>
#include "MS5837.h"
#include <SoftwareSerial.h>



/* Orientation sensor
   Connections
   ===========
   Connect SCL to analog 5
   Connect SDA to analog 4
   Connect VDD to 5V DC
   Connect GND to GND

   SOS sensor 
   Connecitons: (Arduino 1)
   Connect Leak to digital 6 (Arduino 1)
   Connect VDD to 5V DC (Arduino 1)
   Connect GND to GND (Arduino 1)

   Levelconverter
   Connections:
   VDD to 5V  (Arduino 2)
   GND to GND (Arduino 2)
   SCL to SCL (Arduino 2)
   SDA to SDA (Arduino 2)

   VDD to 5V  (Arduino 1)
   GND to GND (Arduino 1)
   SCL to analog 4 (Arduino 1)
   SDA to analog 5 (Arduino 1)

   Pressure sensor
   Connections:
   Connect SDA to Levelconverter SDL
   Connect SCL to Levelconverter SCL
   Connect VDD to Levelconverter VDD
   Connect GND to Levelconverter GND

   Stepper controller rotation
   Connections:
   Motor A + to AIN1 to digital 2 (Arduino 1)
   Motor A - to AIN2 to digital 3 (Arduino 1)
   Motor B + to BIN1 to digital 4 (Arduino 1)
   Motor B - to BIN2 to digital 5 (Arduino 1)

   Stepper controller translation
   Connections:
   Motor A + to AIN1 to digital 9 (Arduino 1)
   Motor A - to AIN2 to digital 8 (Arduino 1)
   Motor B + to BIN1 to digital 7 (Arduino 1)
   Motor B - to BIN2 to digital 6 (Arduino 1)

   SSR Ventil
   Connections: 
   GND to GND (Arduino 2)
   Signal cable to digital 3 (Arduino 2)

   SSR Pump
   Connections:
   GND to GND (Arduino 2)
   Signal cable to digital 4 (Arduino 2)
*/

/* Delay between fresh samples */
uint16_t BNO055_SAMPLERATE_DELAY_MS = 100;

int errorRotation = 10;
int errorRising = 10;  //Change
int pitchAngle = 0;    //Change
int rotationSpeed = 10;
int translationSpeed = 60;
int nrOfSteps = 10;
int nrRound = 1;  //Change



// Number of steps per revolution for our motor
const int stepsPerRevolution = 200;

int depth = 0;       //Variable that checks if desired depth is reached
int maxDepth = 100;  //Change
int minDepth = 10;   //Change

float value = 0;
float voltage = 0;
int minVoltage = 26;  //Change, not under 24V
int delayVolt = 100;
//Orientiation sensor
Adafruit_BNO055 bno = Adafruit_BNO055(55, 0x29, &Wire);

// Initiate stepper motor for rotation and tanslation
Stepper stepperRotation(stepsPerRevolution, 2, 3, 4, 5);
Stepper stepperTranslation(stepsPerRevolution, 9, 8, 7, 6);

//Pressure sensor
MS5837 sensor;

int state = 0;
SoftwareSerial bt(11, 12);
//Initiate all the sensors
void setup() {
  bt.begin(9600);
  Serial.begin(9600);
  
  while (!Serial) delay(10);  // wait for serial port to open!

  Serial.println("Orientation Sensor Test");
  Serial.println("");

  //Initialise the orientation sensor
  if (!bno.begin()) {
    //Orientation sensor not detected
    Serial.print("Ooops, no BNO055 detected ... Check your wiring or I2C ADDR!");
    while (1)
      ;
  }
  
  
  //Initiate pressure sensor
  Serial.println("Starting pressure sensor");

  Wire.begin();

  // Returns true if initialization was successful
  // We can't continue with the rest of the program unless we can initialize the sensor
  while (!sensor.init()) {
    Serial.println("Init failed!");
    Serial.println("Are SDA/SCL connected correctly?");
    Serial.println("\n\n\n");
    delay(5000);
  }

  sensor.setModel(MS5837::MS5837_30BA);
  sensor.setFluidDensity(997);  // kg/m^3 (freshwater, 1029 for seawater)
}

}

//Part of the program that needs to update
void loop() {

  if (bt.available()) /* If data is available on serial port */
  {

    // Reads the data from the serial port
    state = bt.read();
  }
  /*
  Motor rotation:
  A-clockwise
  B-counterclockwise

  Motor translation:
  C-forward
  D-backwards
  */

  if (state == 'A') {
    stepperRotation.setSpeed(rotationSpeed);
    stepperRotation.step(nrOfSteps);
    state = 0;
  } else if (state == 'B') {
    stepperRotation.setSpeed(rotationSpeed);
    stepperRotation.step(-nrOfSteps);
    state = 0;
  } else if (state == 'C') {
    stepperTranslation.setSpeed(translationSpeed);
    stepperTranslation.step(nrOfSteps);
    state = 0;
  } else if (state == 'D') {
    stepperTranslation.setSpeed(translationSpeed);
    stepperTranslation.step(-nrOfSteps);
    state = 0;
  } else if (state == 'P') {
    uint8_t system, gyro, accel, mag = 0;
    bno.getCalibration(&system, &gyro, &accel, &mag);
    //Prints status
    Serial.println();
    Serial.print("Calibration: Sys=");
    Serial.print(system);
    Serial.print(" Gyro=");
    Serial.print(gyro);
    Serial.print(" Accel=");
    Serial.print(accel);
    Serial.print(" Mag=");
    Serial.println(mag);
    Serial.println("--");
    delay(BNO055_SAMPLERATE_DELAY_MS);  //Updates every 100ms
    if (mag == 3 && system == 3 && gyro == 3 && accel == 3) {
      state = 0;
    }
  }  else if (state == 'Z') {
  //Data that should be gathered by the orientation data
  sensors_event_t orientationData, linearAccelData;
  bno.getEvent(&orientationData, Adafruit_BNO055::VECTOR_EULER);  //Data for the degress (divaing, resurfing, rotation, ?heading?)
  //Data gathered from pressure sensor to check depth
  sensor.read();
  Serial.print("Djup= ");
  Serial.println(sensor.depth());

  value = analogRead(A0);
  voltage = 9.2 * ((value * 5.0 / 1024) - 0.55);
  Serial.print("Voltage = ");
  Serial.println(voltage);
  delay(delayVolt);


  //compass(&orientationData);
  //rotationEvent(&orientationData);
  //pitchEvent(&orientationData);


  if (sensor.depth() < maxDepth) {
    pitchAngle = -45;
    rotationEvent(&orientationData);
    pitchEvent(&orientationData);
  } else if (sensor.depth() >= maxDepth) {
    pitchAngle = 45;
    rotationEvent(&orientationData);
    pitchEvent(&orientationData);
  }

  if (sensor.depth() >= maxDepth) {
    depth = depth + 1;
    if (depth >= nrRound) {
      pitchAngle = 45;
      pitchEvent(&orientationData);
      rotationEvent(&orientationData);
    }
    
  }*/
  }
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

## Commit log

2024-07-05 Kalibrering av magnetometer
2024-07-23 atlas command kod UART och I2C
2024-08-12 Made AGT code in void functions instead of case structure
2024-08-13 AGT code
    This code for AGT worked to the point that when unconnected to the ESP, it went to the pickup case and retreived GNSS position succesfully and transmitted an iridium message succesfully. GNSS was of 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
2024-08-15 Update 3. Hardware and CAD.md
2024-08-15 Update 6. Sensors.md
2024-08-15 Update 1. Assembling and initilization.md
2024-09-28 Add files via upload
    'pitch', 'roll', 'yaw', 'depth', 'medianDepth', 'pressure', 'conductivity', 'temperature', 'potentiometer', 'medPot', 'state'
2025-02-25 Uploaded some files
    [PCB power glider v22.brd, PCB power glider v29.f3z, PCB_power_glider_v13.sch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]

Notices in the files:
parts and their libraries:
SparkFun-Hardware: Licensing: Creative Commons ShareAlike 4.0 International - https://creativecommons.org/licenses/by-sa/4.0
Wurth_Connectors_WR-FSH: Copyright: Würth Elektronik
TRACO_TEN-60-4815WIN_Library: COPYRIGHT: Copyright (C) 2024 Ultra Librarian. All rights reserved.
